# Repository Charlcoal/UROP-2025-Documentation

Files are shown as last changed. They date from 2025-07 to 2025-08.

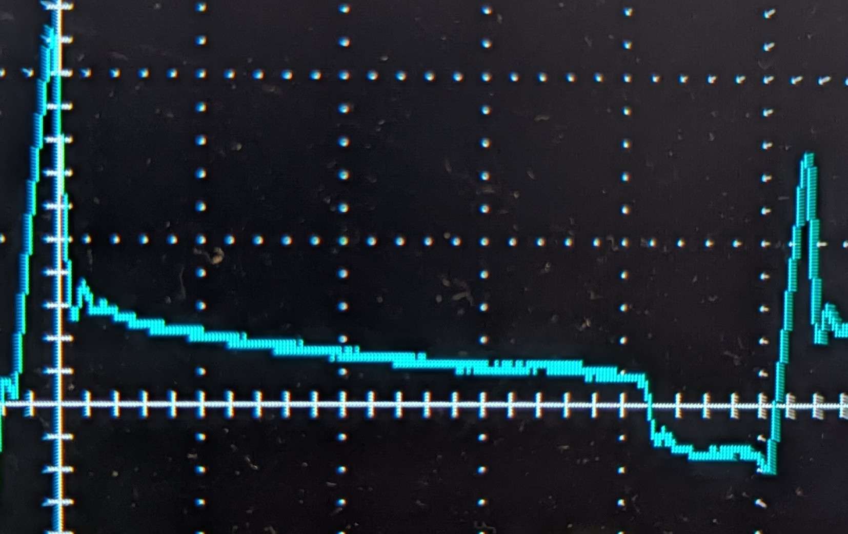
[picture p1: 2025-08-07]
RESEARCH/current_sensing/with_screw.jpg

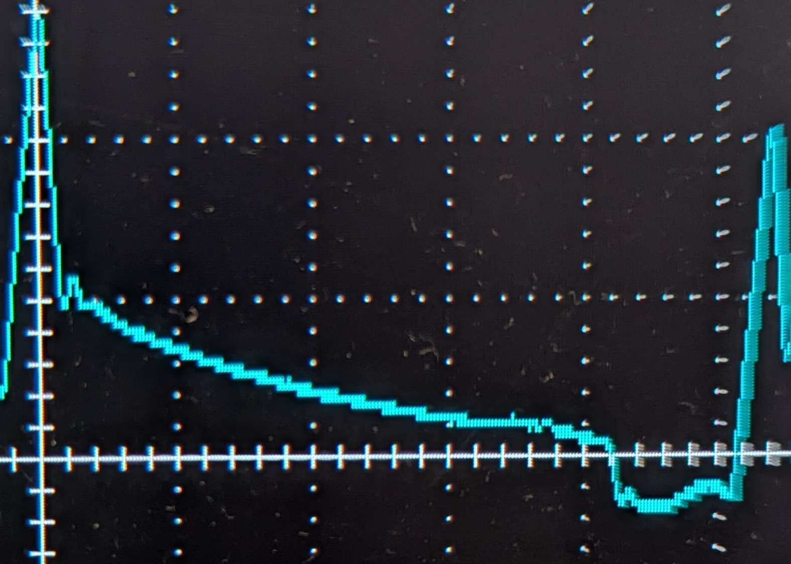
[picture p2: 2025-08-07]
RESEARCH/current_sensing/without_screw.jpg

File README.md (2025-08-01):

# Future Shape Display Mechanisms

This project is investigating the potential of using solenoid
coils to directly drive pins of a shape display,
specifically one that updates in real time (~20Hz) with
~8 bits of distinguishable position. Ideally, it would also
be able to sense force applied to the tops of the pins.

## Sections

**PCB_COIL** contains initial research on the possibility of
printing coils on circuit, which did not get far.  
**RESEARCH** contains the relevant data and analysis
for the project as it stands now.

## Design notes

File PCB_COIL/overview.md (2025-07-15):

# Overview of PCB Coil Research

Coiltest is a folder containing the KiCad files for the test board I printed.
testing.md contains the results of testing this board.

Overall, the strength of interaction between the coils and the magnets was
weak compared to the interaction between the magnets and each other.
I was not confident in the feasibility of creating a pin display using
pcb coils because of this, and switched design towards more "traditional"
electromagnetic coils.

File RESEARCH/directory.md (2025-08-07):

# Directory

[coil_mag_interaction_distance.md](coil_mag_interaction_distance.md)
contains data on the interaction between coils
and the magnet at various distances.

[initial_half_bridge_testing](initial_half_bridge_testing/)
contains the results of prototyping with the
MP6527 Half-Bridge Driver IC, which did not
end with ideal results.

[coil_shielding](coil_shielding/)
contains a quick look into the effectiveness
of shielding the magnets from adjacent pins.

[current_sensing](current_sensing/)
contains development of a working in-line current
sensor, and the resulting current with/without
a magnet present.

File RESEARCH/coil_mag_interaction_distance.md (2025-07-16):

# Interaction Between 300 Turn Coil and N52 Magnet at various distances

## Data, taken at a coil amperage of 0.2 A

| distance from center (inches) | Force (milliNewtons) |
| ---: | ---: |
| -12/16 | 0 |
| -11/16 | 0.5 |
| -10/16 | 0.9 |
| -9/16 | 1.2 |
| -8/16 | 3.0 |
| -7/16 | 4.2 |
| -6/16 | 6.2 |
| -5/16 | 7.8 |
| -4/16 | 10.3 |
| -3/16 | 12 |
| -2/16 | 8.2 |
| -1/16 | 5.6 |
| 0 | 2.5 |
| 1/16 | -5.2 |
| 2/16 | -10.0 |
| 3/16 | -10.5 |
| 4/16 | -8.6 |
| 5/16 | -9.3 |
| 6/16 | -7.2 |

## Methodology

The coil sleeve was suspended above a scale at a specific
distance with a magnet and spacer cylinder inside, such that
the spacer was resting on the scale and the center of the
magnet was a specific distance from the center of the coil.
Then, the scale was zeroed, and the current was turned on.
For values that appear negative here, the polarity was reversed
to provide a consistant downwards force against the scale. The
displayed "mass" in grams is interpreted as milliNewtons here.

## Analysis

To model the interaction between the magnet and the coil,
I treated each center as a point magnetic pole; the magnet
slides along the x axis with a perpendicular offset $$D$$ to the coil.
I am using a point model since the coil length and magnet length
are the same, simlpifying the dynamics of dipoles to monopoles.
The offset accounts for the concentricity of the magnet and coil.

Using some trigonometry, this model predicts the force to be
$$\frac{ax}{(D^2 + x^2)^{3/2}}$$, where $$a$$ is a constant
describing the intensity of the force overall at 0.2 A,
and $$x$$ is the distance between the magnet center and coil
center, and $$D$$ is the above mentioned perpendicular distance.

I put the data from the table into [desmos](https://www.desmos.com/calculator/2qaqsglqw1)
and tried a regression fit onto the equation above.
It did not quite work as expected, as the force measurements
get close to 0 too quickly near the edges. This discrepancy made
me realized my measurement method probably was effected by static friction,
as the magnet did not move while applying force. To counteract this, I added
a correction term $$c$$ to the model, which matched the sign of $x$. This
resulted in a great fit: $$R^2 = 0.989$$. The parameters for the fit
were $$a = 2.50 \text{mN} * \text{in}^2$$, $$D = 0.255$$ inches,
and $$c = 3.90$$ milliNewtons.

When combining 4 of these equation spaced
according to the distance between coils, there are 4 distinct notches in the
total achievable force in the center of each coil. They do not dip below
7 milliNewtons however (from adjacent coils), so with brief 0.8 Amp spikes
in current it should perform fine.

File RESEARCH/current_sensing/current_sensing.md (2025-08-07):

# Current Sensing

## Method

To measure the current of the coils, I used a
~1 Ohm resistor in series with the coil. I then
measured the voltage across the resistor using an
[Op-Amp circuit](circuit.jpg).

The Low-Pass filter was needed to prevent the voltage
spikes from becoming too severe. The voltage spikes
are a side effect of measuring the current in-line,
i.e. the common mode voltage swings by 12 volts every
PWM cycle, causing a noticeable error in the output of
the Op-Amp. Measuring during the free-wheeling section
of the PWM cycles should give accurate results, though.

## Results

With current sensing working, I then tested whether the
presence of a magnet inside the coil effected the current
measured. Unfortunately, there was no distinguishable difference.
I then tested a ferromagnet screw (just an iron/steel screw)
instead, which did have a noticeable difference. I have taken
images of the 256-sample averages of a single PWM cycle [with](with_screw.jpg)
and [without](without_screw.jpg) the screw.

To keep track of the position of the pin in the final design,
both a magnet and some ferromagnetic mass must be integrated
into the pin.

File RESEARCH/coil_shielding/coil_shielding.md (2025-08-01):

# Coil Shielding

The coil shielding was simulated using
[Finite Element Method Magnetics](https://www.femm.info/wiki/HomePage).
The relevant FEM file is included, as well
as 2 screenshots of the coil I am using
in my prototype simulated with and without
shielding. I used 0.02" iron for the simulation,
which resulted in significant reduction in the
magnetic field outside of the shielding, and
a small increase to the fielding within the coil.

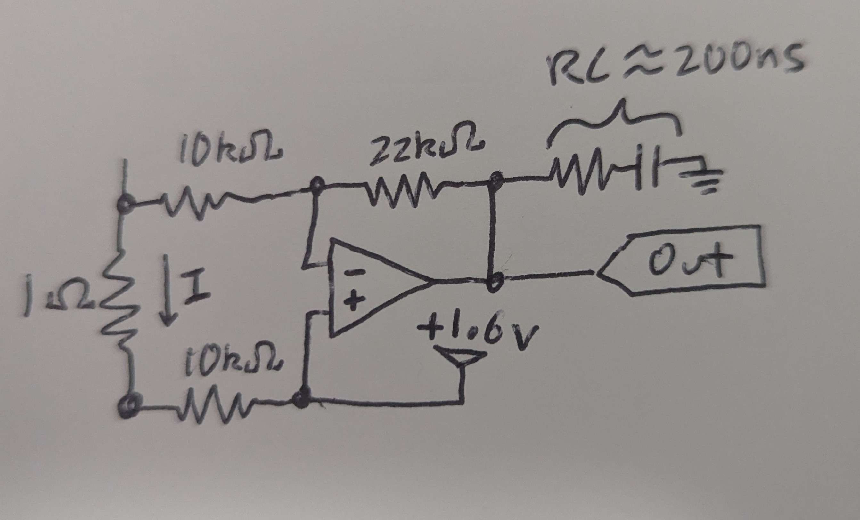
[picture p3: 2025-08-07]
RESEARCH/current_sensing/circuit.jpg

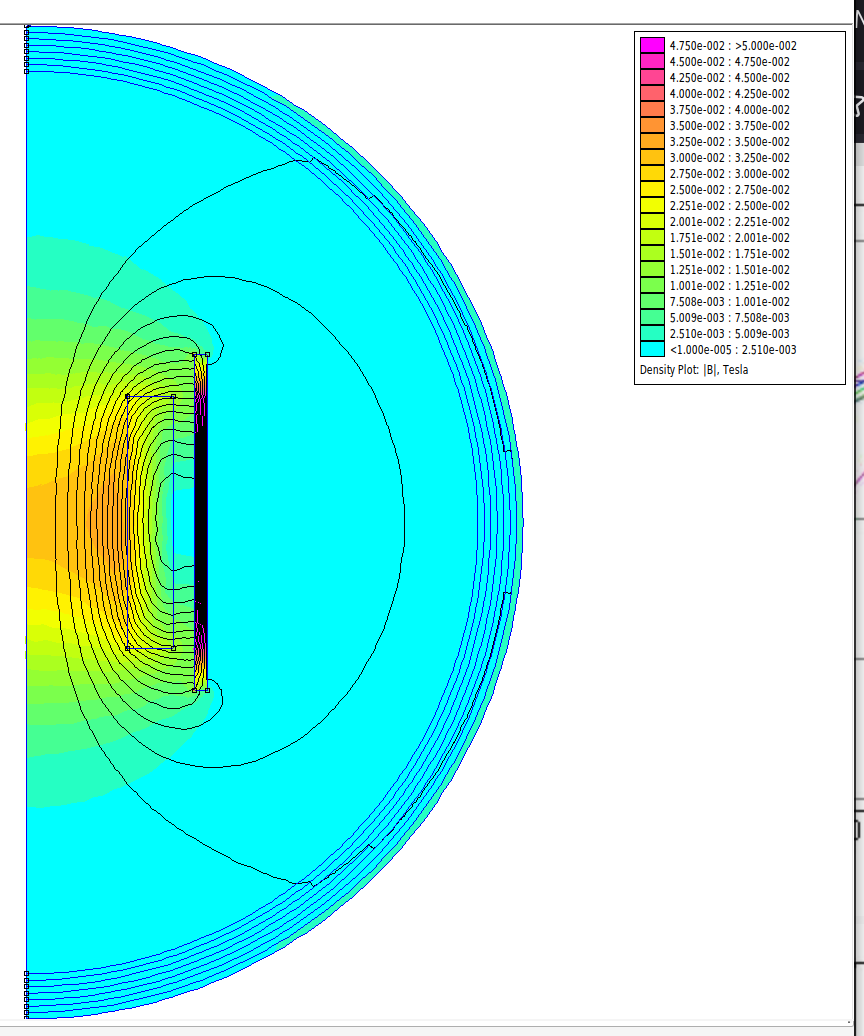
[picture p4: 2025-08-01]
RESEARCH/coil_shielding/0.02"_iron_shielding.png

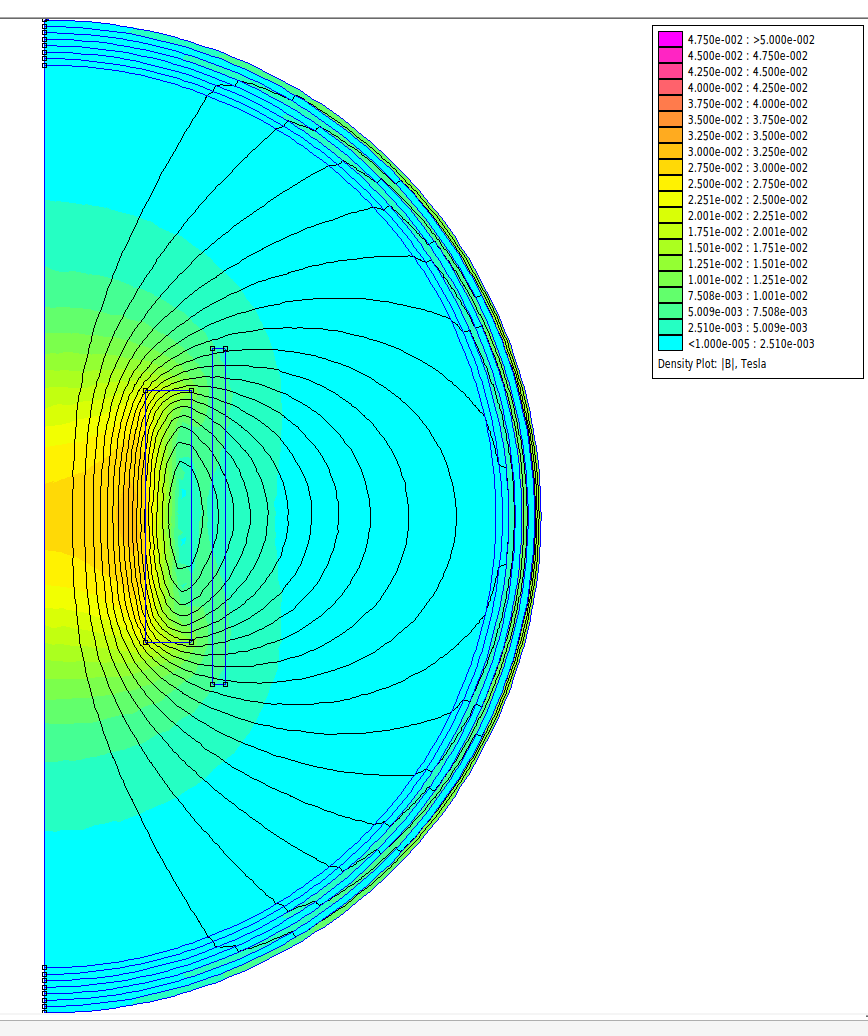
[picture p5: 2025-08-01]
RESEARCH/coil_shielding/no_shielding.png

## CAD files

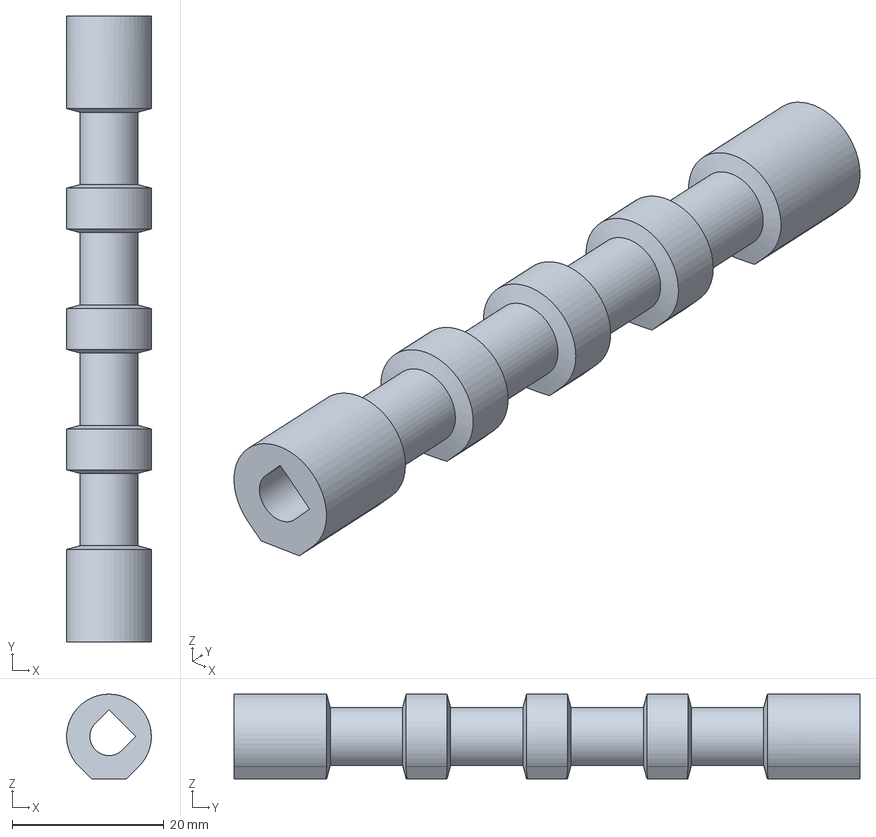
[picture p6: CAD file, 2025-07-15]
Cad_Files/PinSleeve.FCStd
11.2 x 82.6 x 11.2 mm

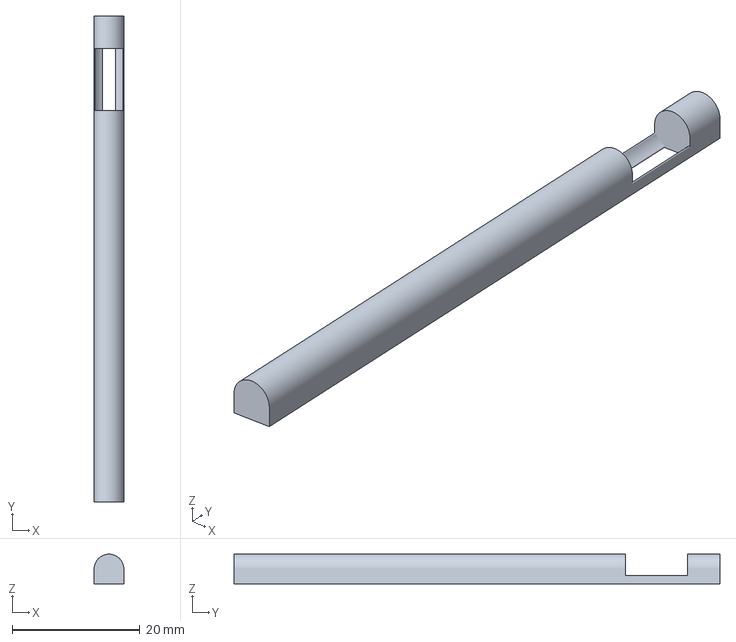
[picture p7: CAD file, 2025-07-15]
Cad_Files/Pin-Rev1.amf
4.66 x 76.2 x 4.66 mm

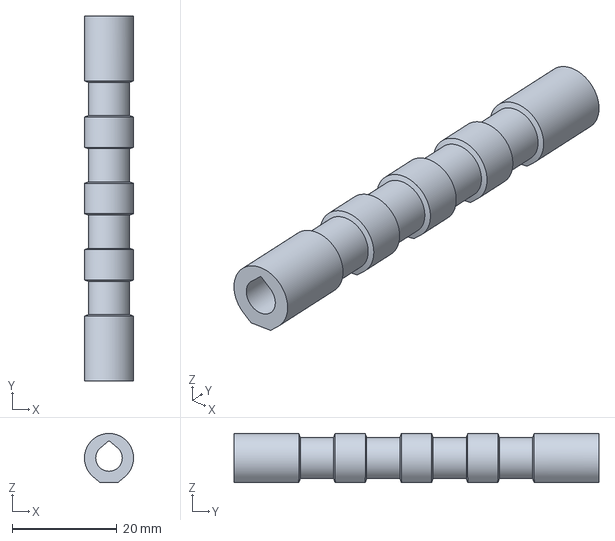
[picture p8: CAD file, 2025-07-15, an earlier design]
Cad_Files/PinSleeve-Rev1.amf
9.40 x 69.8 x 9.40 mm

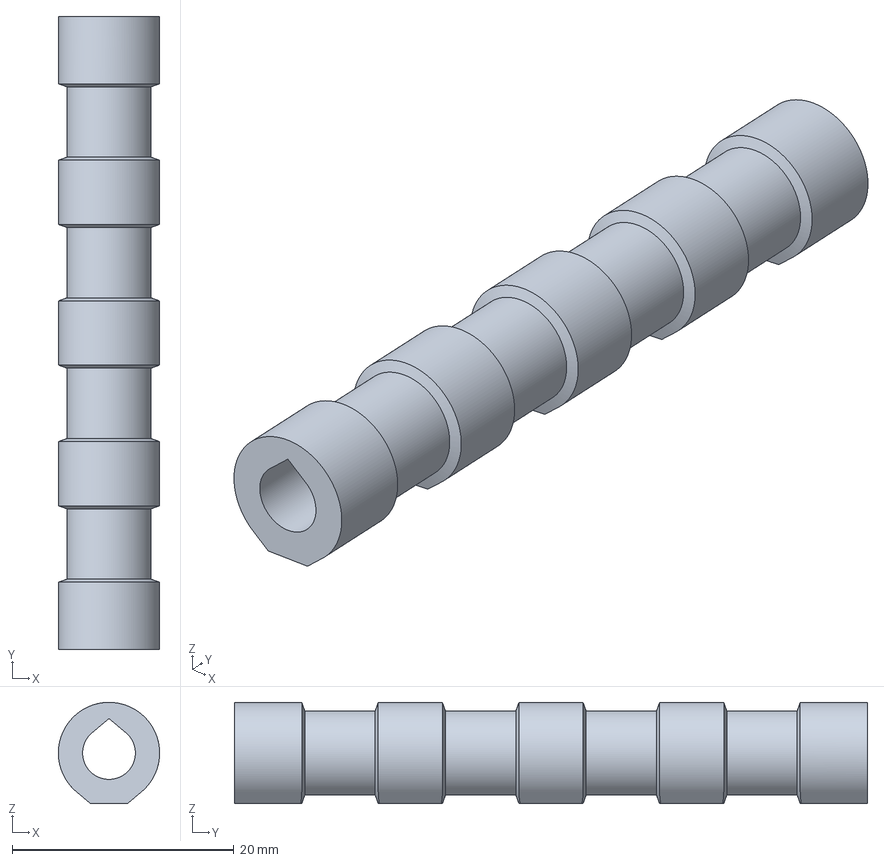
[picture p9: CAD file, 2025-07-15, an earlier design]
Cad_Files/PinSleeve-Rev0.amf
9.14 x 57.1 x 9.14 mm

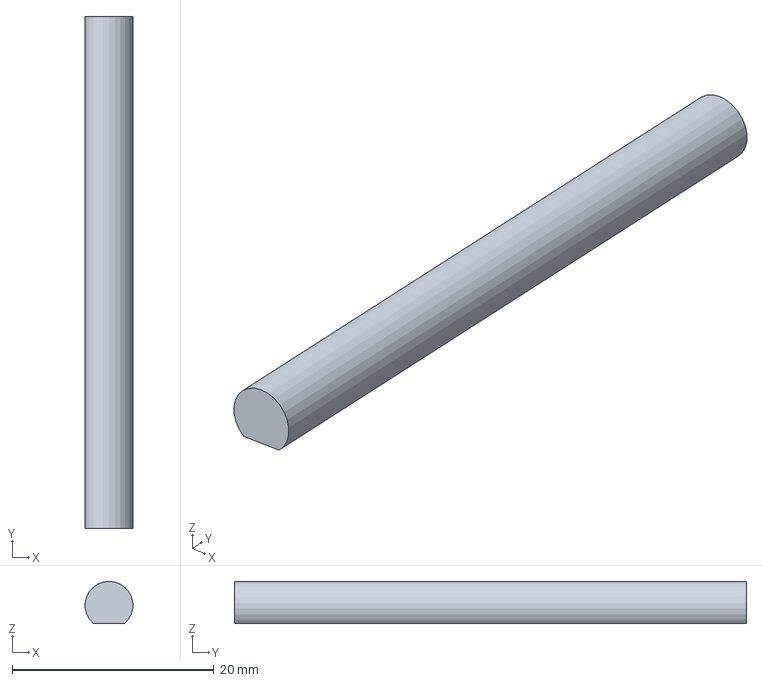
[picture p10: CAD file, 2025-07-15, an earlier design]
Cad_Files/Pin-Rev0.amf
4.74 x 50.8 x 4.21 mm

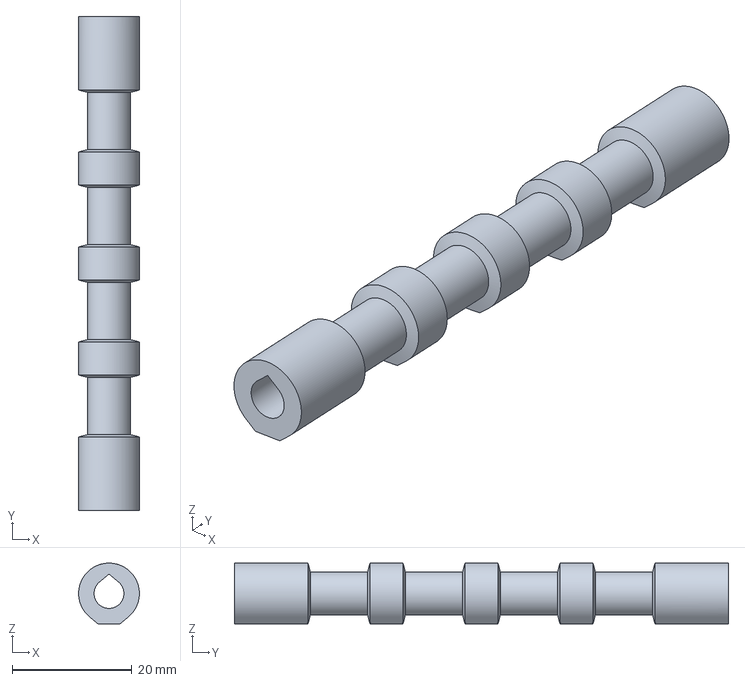
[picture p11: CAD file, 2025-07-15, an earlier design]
Cad_Files/PinSleeve-Rev2.amf
10.2 x 82.5 x 10.2 mm

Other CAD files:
Cad_Files/PinSleeve-Rev3.amf
Cad_Files/Pin.FCStd

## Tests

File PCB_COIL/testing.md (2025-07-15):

# Measurements from test print of pcb coils

## Using 3/16" diameter x 3/8" width N52 axial Cylinder magnet

| Coil | Description | Diameter (cm) | Resistance (Ohms) | Holding Amperage | Holding Wattage | Holding amp-turns | Holding Power Density (W/cm^2) |
| ---- | --- | ---: | ---: | ---: | ---:| ---: | ---: |
| A | 2 layer, 16 turns/layer, 0.15mm W | 1.6 | 5.7 | 0.17 | 0.165 | 5.44 | 0.095  |
| B | 4 layer, 16 turns/layer, 0.15mm W | 1.6 | 10.6 | 0.09 | 0.086 | 5.76 | 0.050  |
| C | 2 layer, 13 turns/layer, 0.23mm W | 1.6 | 2.7 | 0.23 | 0.143 | 5.98 | 0.083  |
| D | 4 layer, 13 turns/layer, 0.23mm W | 1.6 | 5.4 | 0.11 | 0.065 | 5.72 | 0.038  |
| E | 4 layer, 11 turns/layer, 0.30mm W | 1.6 | 3.4 | 0.13 | 0.057 | 5.72 | 0.033  |
| F | 4 layer, 9 turns/layer, 0.15mm W  | 1.2 | 5.7 | 0.12 | 0.082 | 4.32 | 0.097  |
| G | 4 layer, 7 turns/layer, 0.23mm W  | 1.2 | 2.8 | 0.17 | 0.081 | 4.76 | 0.095  |
| H | 4 layer, 6 turns/layer, 0.30mm W  | 1.2 | 1.8 | 0.19 | 0.065 | 4.56 | 0.077  |
| I | 4 layer, 6 turns/layer, 0.15mm W  | 1.0 | 3.4 | 0.17 | 0.098 | 4.08 | 0.195  |
| J | 4 layer, 5 turns/layer, 0.23mm W  | 1.0 | 1.7 | 0.21 | 0.075 | 4.20 | 0.149  |
| K | 4 layer, 4 turns/layer, 0.30mm W  | 1.0 | 1.0 | 0.25 | 0.063 | 4.00 | 0.124  |

### Holding Amperage

The tests were performed by dropping an axial N52 magnet down an aluminum tube,
which was positioned in the center of the pcb coil being tested. The eddy currents
in the aluminum tube would slow the magnet's descent to a consistent (slow) speed.
This was repeated with increasing current through the coil, until the magnet did
not drop completely through the tube. Then current was then recorded.

### Resistance

A standard multimeter was used to find the coil resistance, with compensation for
contact resistance.

### Other Values

All other values have been calculated from the measured values and descriptions
of the coils.

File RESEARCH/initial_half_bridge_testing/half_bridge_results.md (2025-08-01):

# Half Bridge Results

The ~25us rise and fall time of the half bridge
limits the PWN frequency to under 20kHz, meaning
it is audible. Additionally, the switching time
takes up a considerable portion of 10kHz PWM,
significantly impacting the in-line current sensing
with voltage swings. Because the coils are around
450 uH and have a resistance around 6 Ohms, the
10kHz PWN completely fails to create a smooth current,
massively reducing efficiency.

Ideally, a future iteration of this project would use
a discrete gate driver and MOSFETs, with high-side
current sensing, ideally above 20kHz. I think a
functional prototype is still possible with the
MP6527, however. I will be increasing the in-line
current sensing resistance.

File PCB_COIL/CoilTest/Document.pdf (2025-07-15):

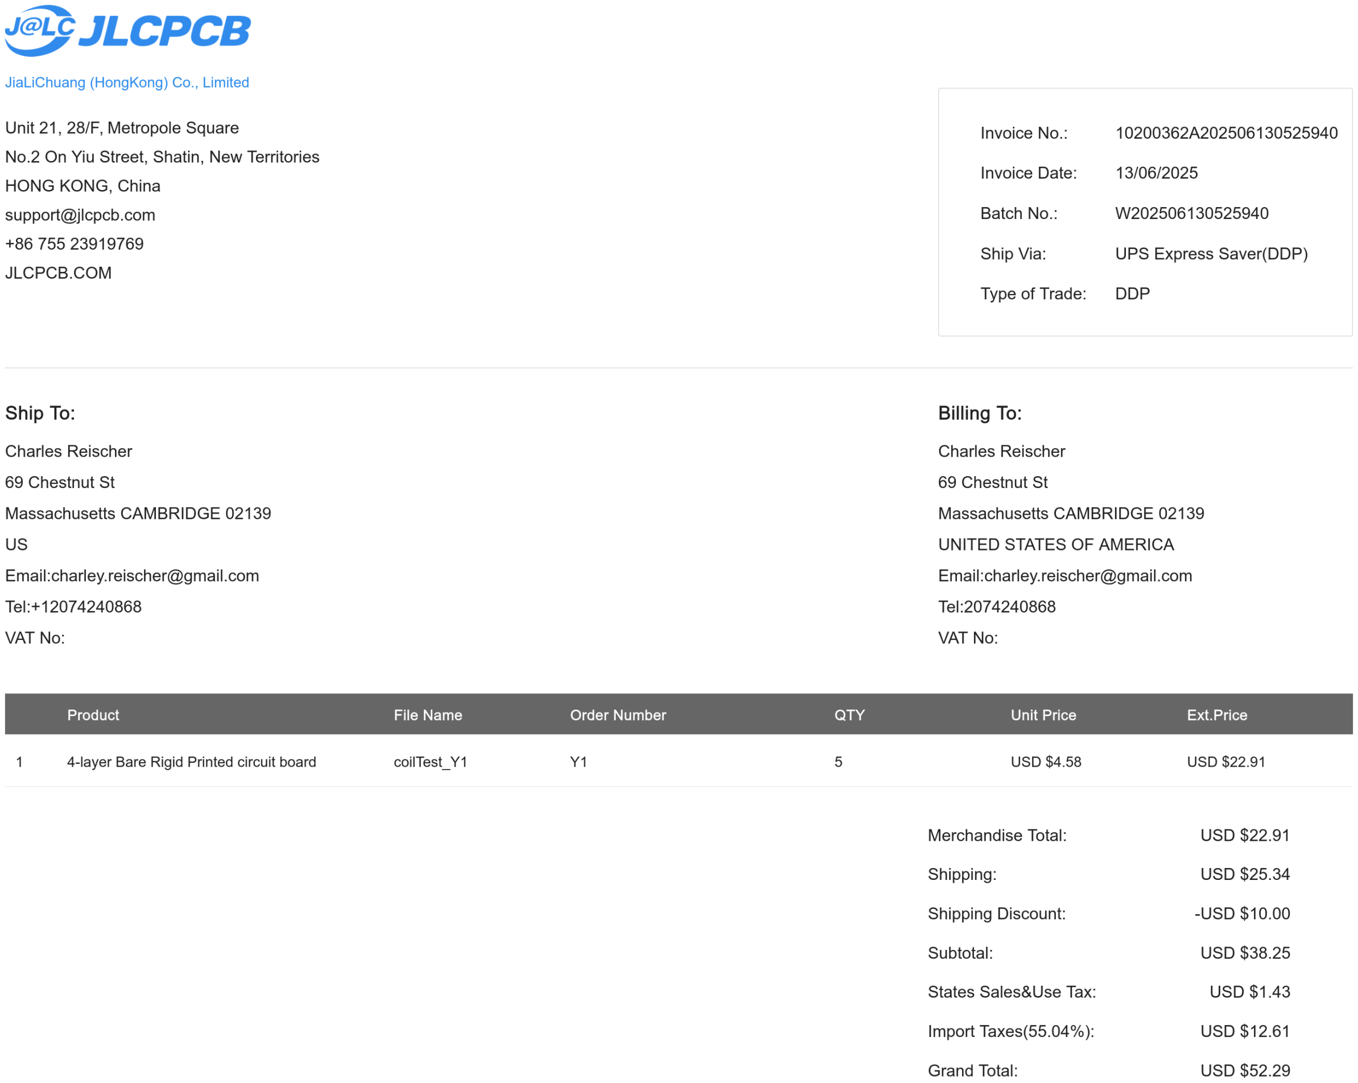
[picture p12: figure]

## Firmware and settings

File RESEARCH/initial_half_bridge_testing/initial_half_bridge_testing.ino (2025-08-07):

#include <SPI.h>

void setup() {
  // put your setup code here, to run once:
  pinMode(2, OUTPUT);
  PORTD |= 0b00000100;
  SPI.begin();
  Serial.begin(115200);
}

void loop() {
  // put your main code here, to run repeatedly:

  uint16_t spiOutput1;
  uint16_t spiOutput2;
  delayMicroseconds(50);

  SPI.beginTransaction(SPISettings(5000000, MSBFIRST, SPI_MODE1));
  //digitalWrite(10, LOW);
  PORTD &= 0b11111011;
  spiOutput1 = SPI.transfer16(0b0000000110000010);
  PORTD |= 0b00000100;

  delayMicroseconds(48);

  PORTD &= 0b11111011;
  spiOutput2 = SPI.transfer16(0b0000000110000110);
  PORTD |= 0b00000100;
  SPI.endTransaction();

  //Serial.print("\n");
  //Serial.print(spiOutput2, BIN);
  //Serial.print("\n");
  //Serial.print("\n");
  //Serial.print(spiOutput1, BIN);
}

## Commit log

2025-07-15 added pcb coil measurement table
2025-07-15 added KiCad files and clarified info
    [CoilTest-B_Cu.gbl, CoilTest-B_Mask.gbs, CoilTest-B_Paste.gbp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]
2025-07-15 included cad files
    [Pin-Rev0.amf, Pin-Rev1.amf, Pin.FCStd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]
2025-07-16 coil magnet interaction research
2025-07-18 put together breakout boards
2025-08-07 current sensing
